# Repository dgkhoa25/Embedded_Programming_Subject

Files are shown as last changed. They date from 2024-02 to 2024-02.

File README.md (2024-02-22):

This project is created based on the subject named "Embedded Programming" (Lập trình nhúng).

The name of project is "Designing a remote vehicle control model via rf and bluetooth protocol".

******************************** ABSTRACT ********************************

  - Helps in basic understanding of ST microcontrollers by controlling single components such as motor control, multi-state programming, and wireless communication setup.
  - Create a general overview model so we can visualize the design for an embedded system, which is essentially just simple parts assembled to suit.
  - Give team members the opportunity to learn basic wireless protocol standards and hardware programming for the system.

******************************** VIDEO DEMO ********************************
 
Link Youtube: https://youtu.be/idwfzNZjZEc?si=ZoLyBULExPPUORM8

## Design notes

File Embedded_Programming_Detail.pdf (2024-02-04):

Báo cáo đồ án Lập trình nhúng

THIẾT KẾ MÔ HÌNH ĐIỀU KHIỂN XE TỪ XA

THÔNG QUA GIAO THỨC RF VÀ BLUETOOTH

Danh sách sinh viên thực hiện

Họ và tên: | Mã số sinh viên

▪

### 1. Giới thiệu (2đ)

### 1.1 Mục đích đề tài:

- Nhằm ôn lại kiến thức đã học trên lớp để thiết kế một mô hình xe có thể điều khiển thông qua hai giao thức là RF và Bluetooth.
- Nhằm tìm hiểu các ngoại vi thông dụng khác của vi điều khiển STM32F103C8T6 như UART, SPI, ADC…. Đồng thời, tìm hiểu thêm cách thức truyền thông không dây cơ bản cho một hệ thống nhúng.
- Nhằm thực hiện mô hình hóa ý tưởng điều khiển xe ô tô thông qua các giao thức chuẩn cơ bản. Cũng như sau này, là nền tảng để bắt đầu trong lĩnh vực Automotive.

1.2 Ý nghĩa đề tài:

- Giúp cho việc hiểu cơ bản về vi điều khiển của hãng ST bằng cách điều khiển các thành phần đơn như điều khiển động cơ, lập trình nhiều trạng thái, thiết lập truyền thông không giây.
- Tạo mô hình khái quát chung để chúng ta có thể hình dung về việc thiết kế cho một hệ thống nhúng, bản chất chỉ là những phần đơn giản lắp ghép lại sao cho phù hợp.
- Giúp các thành viên trong nhóm có cơ hội tìm hiểu các chuẩn giao thức không dây cơ bản và lập trình phần cứng cho hệ thống.

### 2. Cơ sở lý thuyết (2đ) 2.1 Hệ thống xung clock của vi điều khiển

- Cách cấu hình xung Clock trên STMCubeMX.
- Cách chia tần số xung Clock khi cấu hình xuất xung PWM (tần số được sử dụng trong đề tài là 1 kHz).
- Cách thức hoạt động của ngắt System timer 24 bit đếm xuống.

### 2.2 Hệ thống ngoại vi của vi điều khiển

- Cách cấu hình Port/Pin vào ra trên STMCubeMX
- Cách thức hoạt động của các thanh ghi cấu hình GPIO như thanh ghi CRL, CRH, BSRR…
- Cách đọc các trạng thái phím nhấn cũng như mức logic ở các ngõ vào/ra sao cho phù hợp với mức logic của vi điều khiển.

### 2.3 Hệ thống truyền thông

- Hiểu cơ bản cách hoạt động của các bộ UART, SPI để cấu hình và sử dụng các hàm từ thư viện HAL

- Cách thức truyền nhận một chuỗi và xử lí chuỗi để thực hiện các công việc điều khiển.

### 2.4 Hệ thống ngoại vi Analog/Digital Convert

- Hiểu được cách hoạt động của bộ ADC và các cách đọc từng kênh.
- Thực hiện mapping giá trị vào các ngưỡng.

### 2.5 Hệ điều hành nhúng Embedded Operating System

- Hiểu cách cấu hình và chọn giá trị khoảng thời gian cho các tiến trình(TASK)

### 3. Thiết kế phần cứng (2đ) 3.1 Sơ đồ khối:

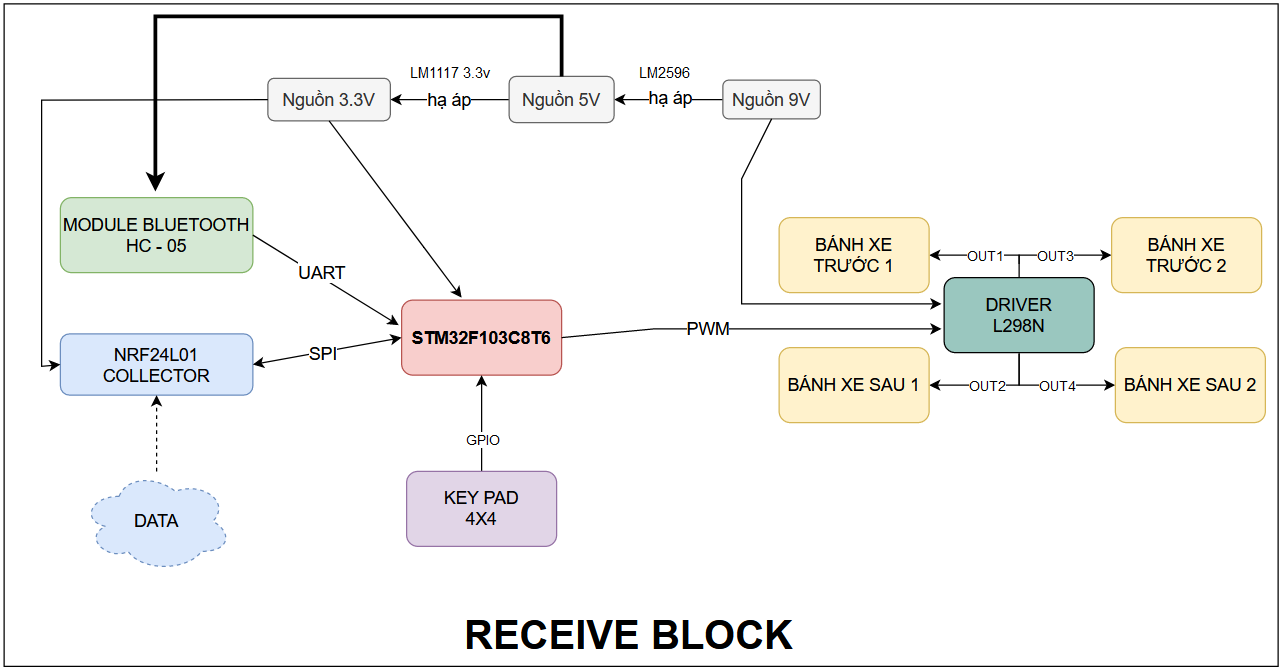
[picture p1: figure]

Hình 1: Sơ đồ khối của khối nhận sử dụng STM32F103C8T6

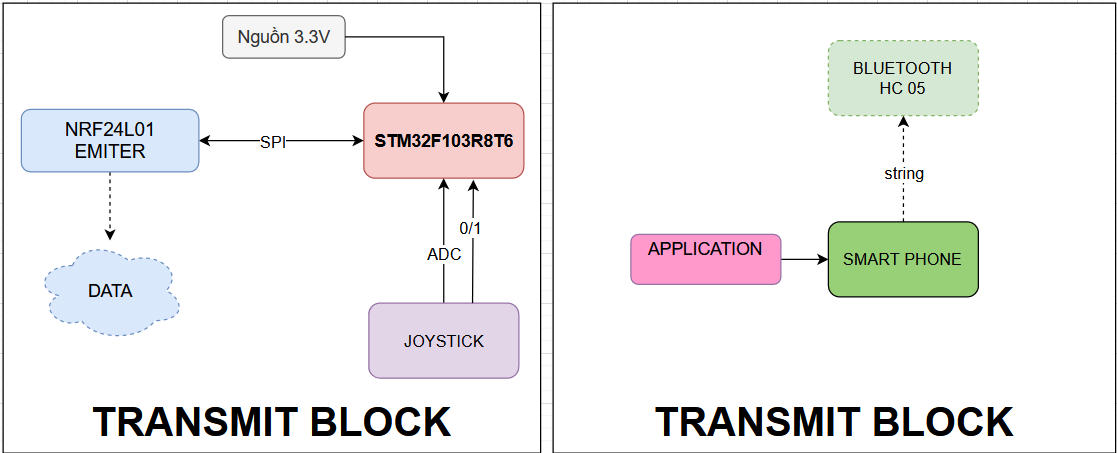
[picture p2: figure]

Hình 2: Sơ đồ khối của hai khối truyền dữ liệu sử dụng STM32F103R8T6 Giải thích sơ đồ khối: gồm có 2 khối chính là khối nhận và khối truyền dữ liệu
3.1.1 Khối nhận và xử lí tín hiệu:
- Khối nguồn: Sử dụng nguồn pin 9V để cấp cho 4 động cơ giảm tốc, tiếp tục hạ áp từ 9V xuống 5V để cấp cho module Bluetooth HC 05, tiếp tục thực hiện hạ áp từ 5V xuống 3.3V đê cấp cho vi điều khiển STM32F103C8T6 và module NRF24L01.
- Khối Vi điều khiển STM32F103C8T6: Vi điều khiển thực hiện nhận tín hiệu không dây và xử lí các tiến trình như kiểm tra KEYPAD, phân tích chuỗi kí tự, định thời chương trình, băm xung PWM…
- Khối Blutooth HC05: nhận chuỗi tín hiệu từ ứng dụng điều khiển trên điện thoại và thực hiện gửi vào vi điều khiển thông qua giao thức UART.
- Khối NRF24L01: nhận tín hiệu từ khối truyền và thực hiện gửi chuỗi kí tự thông qua giao thức SPI.
- Khối Driver L298N: nhận tín hiệu xung PWM từ vi điều khiển để cho ra dải điện áp khác nhau làm thay đổi tốc độ động cơ.
3.1.2 Khối truyền tín hiệu:
- Khối nguồn: nguồn cấp 3.3V lấy từ USB mạch nạp ST-Link V2.
- Khối vi điều khiển STM32F103R8T6: Vi điều khiển thực hiện gửi chuỗi kí tự điều hướng dựa vào tiến trình xử lí Joystick. Joystick sẽ được đọc tín hiệu vào MCU thông qua kênh ADC 12 bit và một nút nhấn tích hợp sẵn trên Joystick để thực hiện chuyển đổi qua lại giữa 2 sóng Blutooth và RF.
- Khối Smartphone: được cài sẵn ứng dụng Bluetooth RC Controller. Khi kết nối với thành công với điện thoại sẽ bấm các nút điều hướng trên giao diện để gửi chuỗi kí tự xuống HC 05.

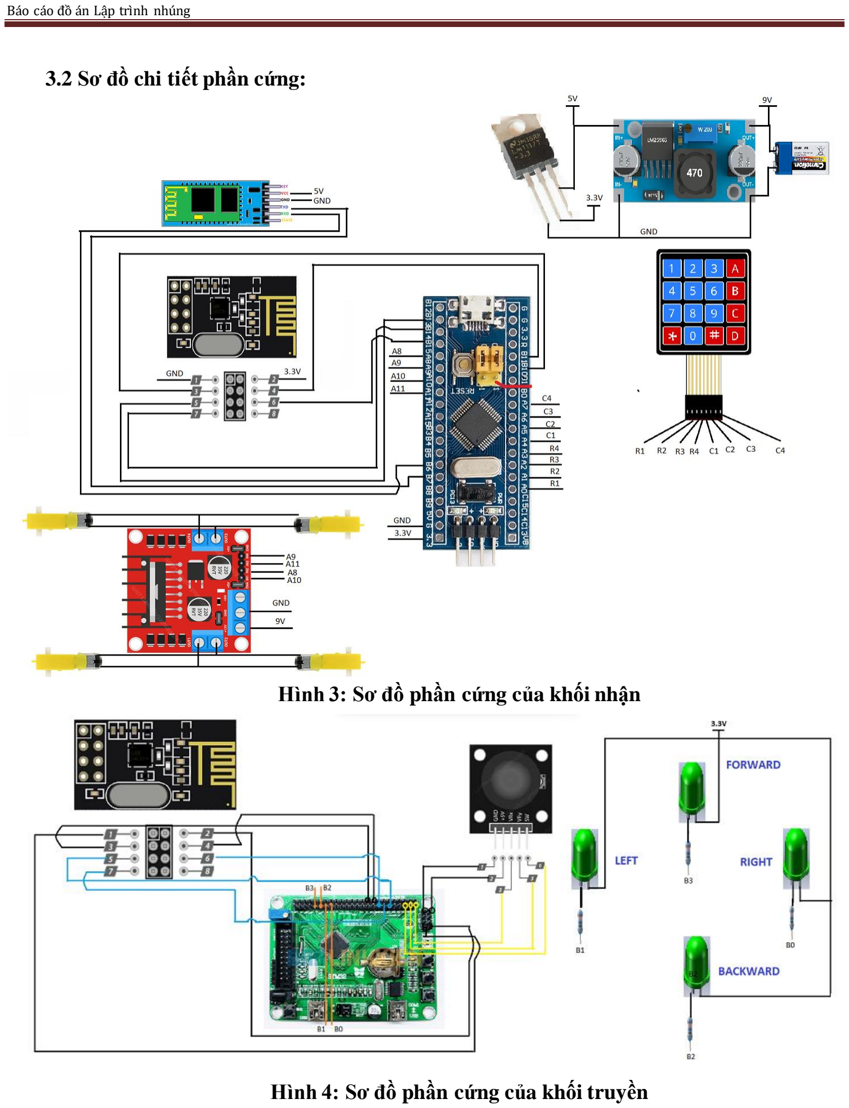
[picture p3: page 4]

### 3.2 Sơ đồ chi tiết phần cứng:

Hình 3: Sơ đồ phần cứng của khối nhận

Hình 4: Sơ đồ phần cứng của khối truyền

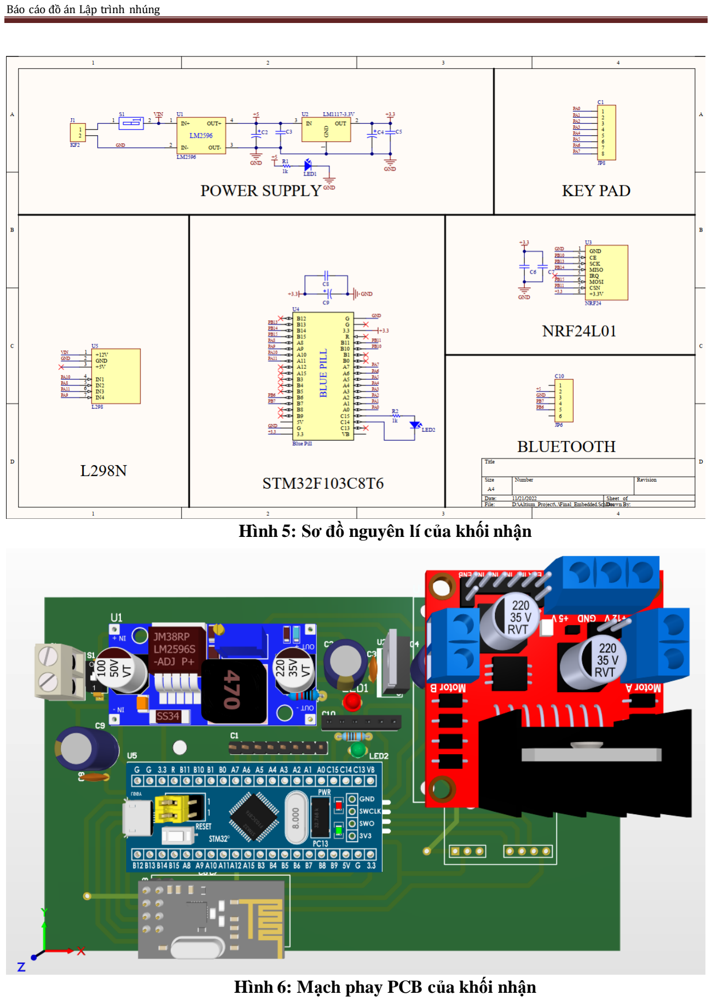
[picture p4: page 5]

Hình 5: Sơ đồ nguyên lí của khối nhận

Hình 6: Mạch phay PCB của khối nhận

Giải thích sơ đồ nguyên lí:
- Khối nguồn cấp vào: sử dụng 2 pin Li-on 4.2V cấp nguồn cho driver L298. Qua mạch hạ áp LM2596 còn 5V để cấp cho Bluetooth HC 05. Tiếp tục hạ áp qua LM1117-3.3V để cấp cho vi điều khiển và NRF24L01.
- Khối vi điều khiển STM32F103C8T6:
+ Các chân A0 – A3(Output), A4 - A7(Input) dùng cho chức năng quét KEYPAD 4x4 + Các chân A8 nối với IN2, A9 nối với IN4, A10 nối với IN1, A11 nối với IN3 trên driver L298.
+ Chân A7 nối với Rx, chân A6 nối với Tx của moudule Bluetooth HC 05.
+ Chân B10 nối với chân CE, B11 nối với chân CSN, B13 nối với chân SCK, B14 nối với chân MISO, chân B15 nối với chân MOSI của module NRF24L01.
+ Chân C14 và C15 mắc nối tiếp với 1 LED và 1 điện trở để tạo tín hiệu khi cần.

### 4. Thiết kế phần mềm (2đ) 4.1 Lưu đồ chương trình trạm thu – Receive Blcok:

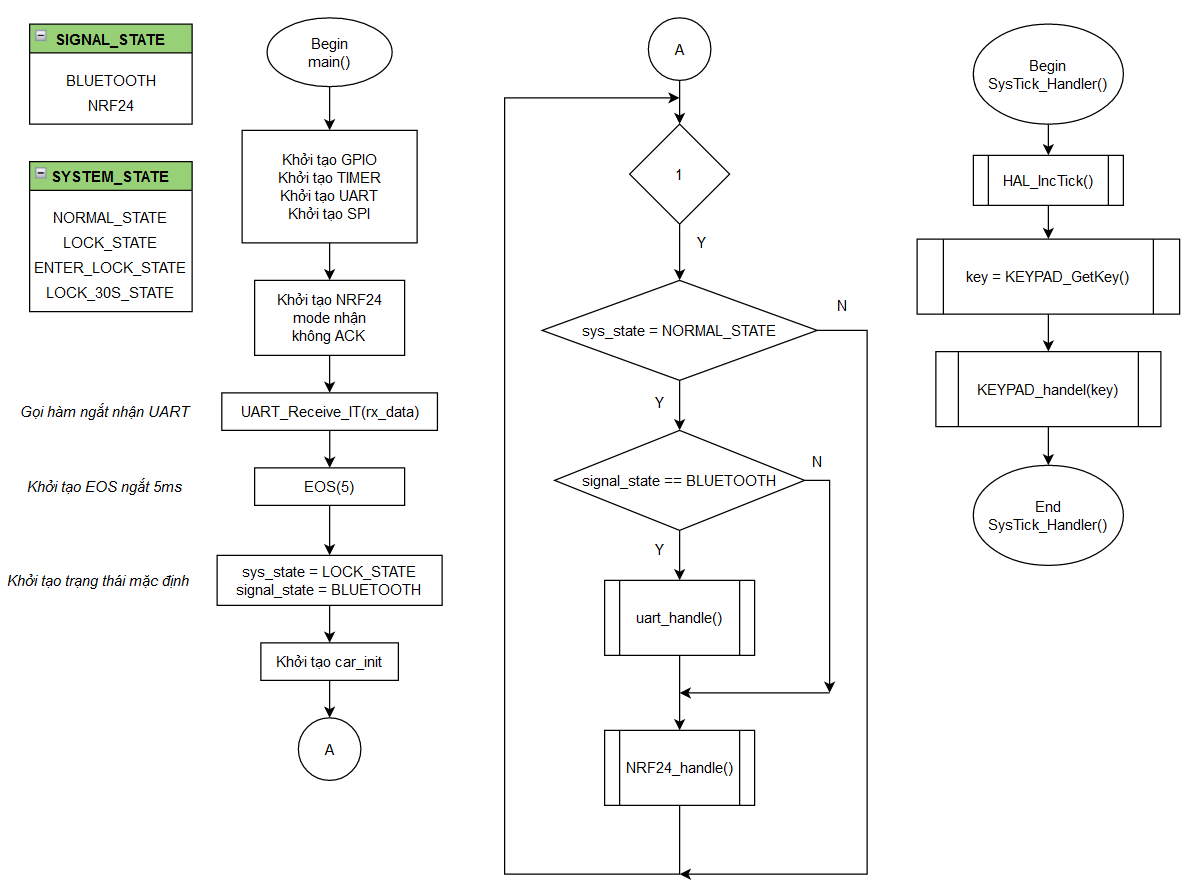
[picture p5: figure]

Hình 7: Lưu đồ chương trình chính trong file main.c (1) Giải thích: Hệ thống sẽ chờ được mở khóa(NORMAL_STATE) để tiếp nhận các tín hiệu điều khiển. Ngoài ra hệ thống còn khởi tạo hệ điều hành nhúng EOS với chu kỳ ngắt 5ms để thực hiện quét KEYPAD và các hàm thực thi KEYPAD.
Mặc định hệ thống sẽ được điều khiển thông qua tín hiệu Bluetooth. Nếu nút nhấn trên Transmit Block được nhấn thì sẽ chuyển sang điều khiển tín hiệu NRF24 và ngược lại.

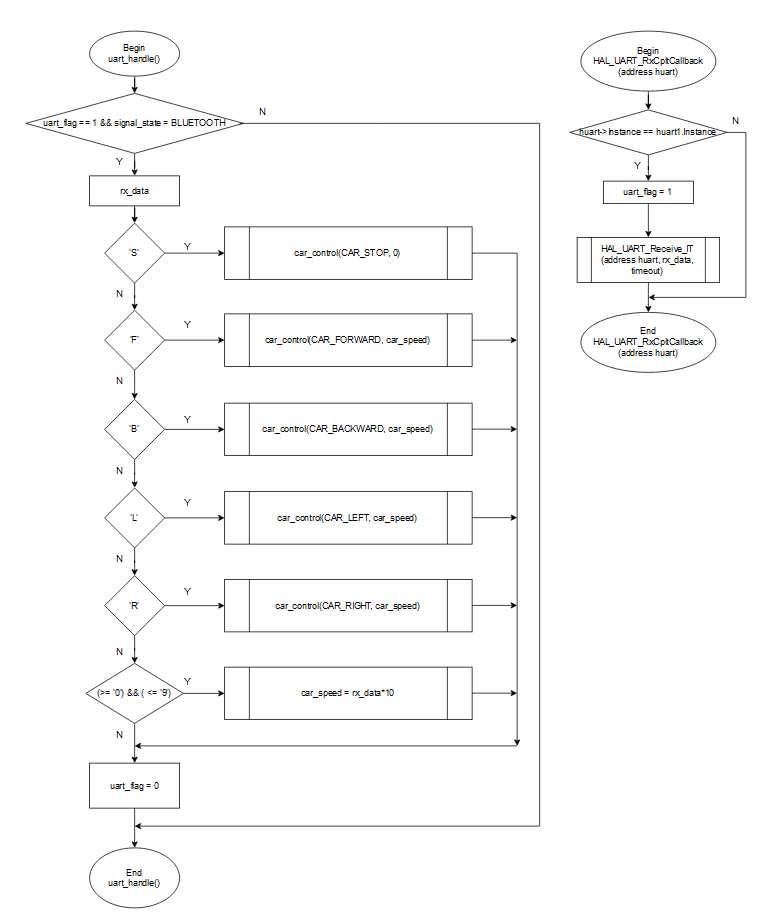
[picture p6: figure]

Hình 8: Lưu đồ chương trình con trong file main.c (2) Giải thích: Chương trình này sẽ kiểm tra biến cờ(uart_flag) nhận dữ liệu và có đang ở trong trạng thái tín hiệu điều khiển bằng Bluetooth không. Nếu cả 2 đúng thì thực hiện giải mã dữ liệu từ UART gửi đến. Hình bên trái là hàm ngắt nhận UART khi có kí tự gửi đến sẽ xảy ra ngắt, gán vào biến rx_data và đặt cờ uart_flag = 1.

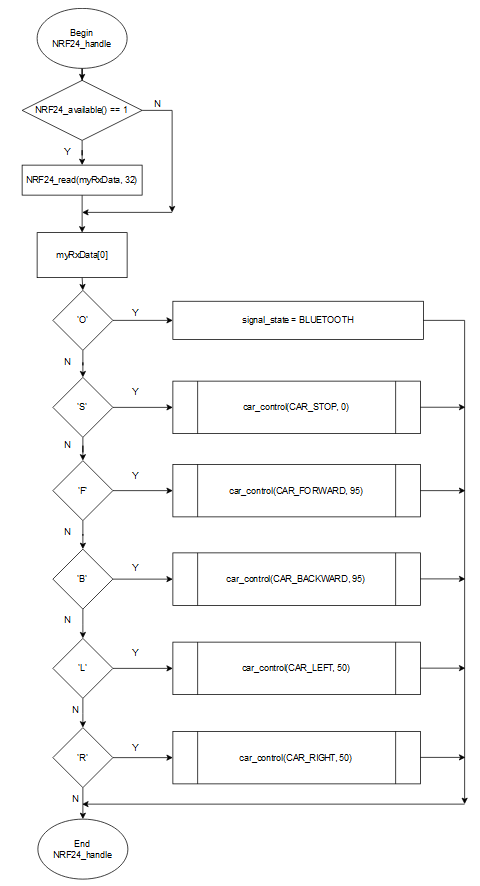
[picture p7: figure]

Hình 9: Lưu đồ chương trình con trong file main.c (3) Giải thích: Chương trình này sẽ lắng nghe có tín hiệu NRF24 gửi đến hay không (hàm NRF24_available()), nếu có tín hiệu thì sẽ thực hiện giải mã kí tự đã nhận để điều khiển xe. Do khối Transmit Block đã cấu hình gửi 1 kí tự nên chỉ cần sử dụng dữ liệu mảng đầu tiên để thực hiện điều khiển. Kí tự ‘O’ để hệ thống bật chế độ điều khiển Bluetooth.

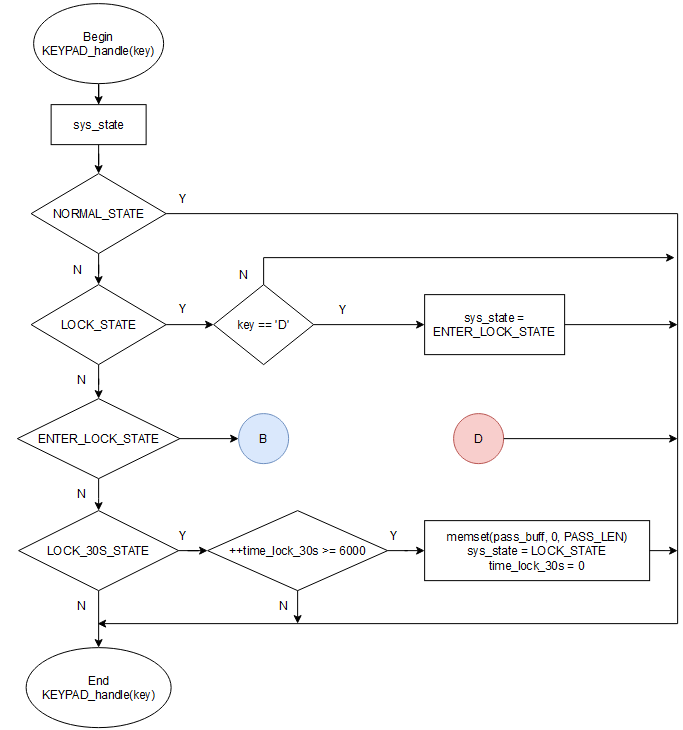
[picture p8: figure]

Hình 10: Lưu đồ chương trình con trong file main.c (4) Giải thích: Chương trình này dùng để nhập mật khẩu khởi động xe. Với mật khẩu được định nghĩa sẵn là “12345678”. Khi nhấn phím D thì sẽ vào trạng thái cho phép nhập mật khẩu. Khi đã vào trạng thái ENTER_LOCK_STATE sẽ thực hiện các công việc được trình bày riêng ở phần tiếp theo. Nếu mật khẩu đúng thì sẽ mở khóa xe(NORMAL_STATE), nếu sai thì xe sẽ bị khóa 30 giây. Khi 30 giây kết thúc quay lại trạng thái LOCK_STATE, đồng thời thực hiện reset giá trị các phần tử trong mảng bằng hàm memset để chờ nhập mật khẩu mới.

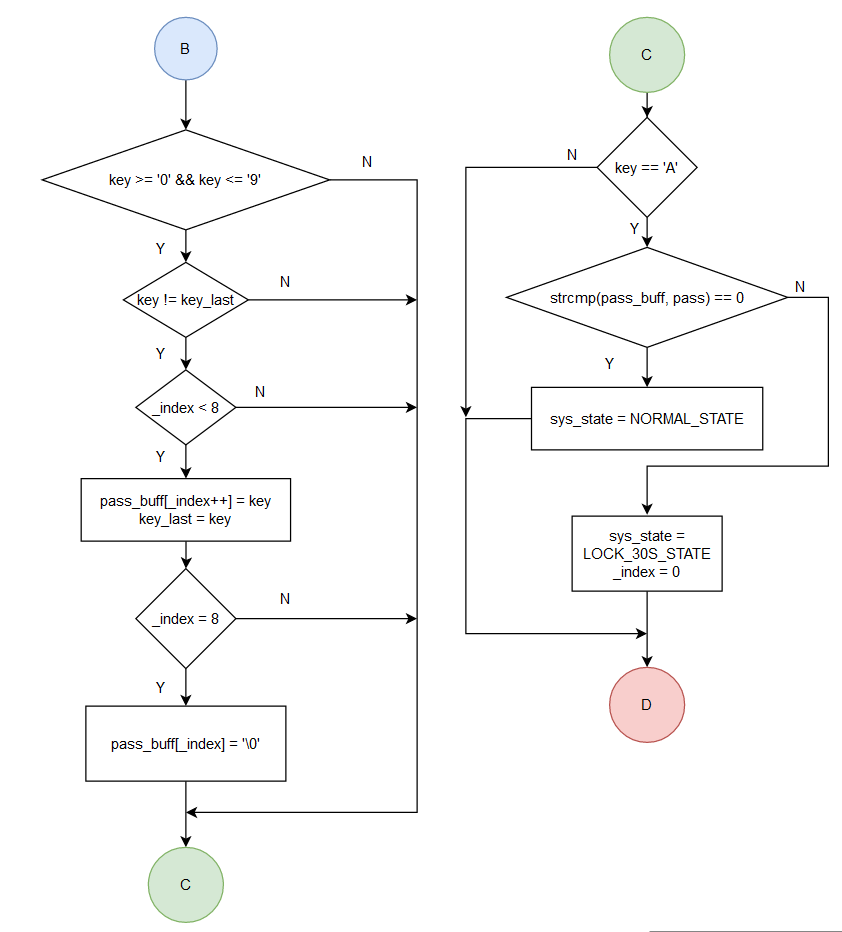
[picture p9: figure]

Hình 11: Lưu đồ giải thuật chương trình con trong file main.c (5) Giải thích: Chương trình này thực hiện đọc giá trị biến key để tiến hành đẩy kí tự vào một mảng đệm (hay mật khẩu của người dùng nhập) gồm 8 phần tử và thêm một phần tử thứ 9 là ‘\0’ để tạo thành một chuỗi. Sau đó nhấn phím A để kiểm tra và sử dụng hàm strcmp trong thư viện string.h để so sánh. Nếu mật khẩu định nghĩa sẵn và mật khẩu đã nhập đúng thì thực hiện mở khóa(NORMAL_STATE), nếu sai thì chuyển sang trạng thái LOCK_30S_STATE.

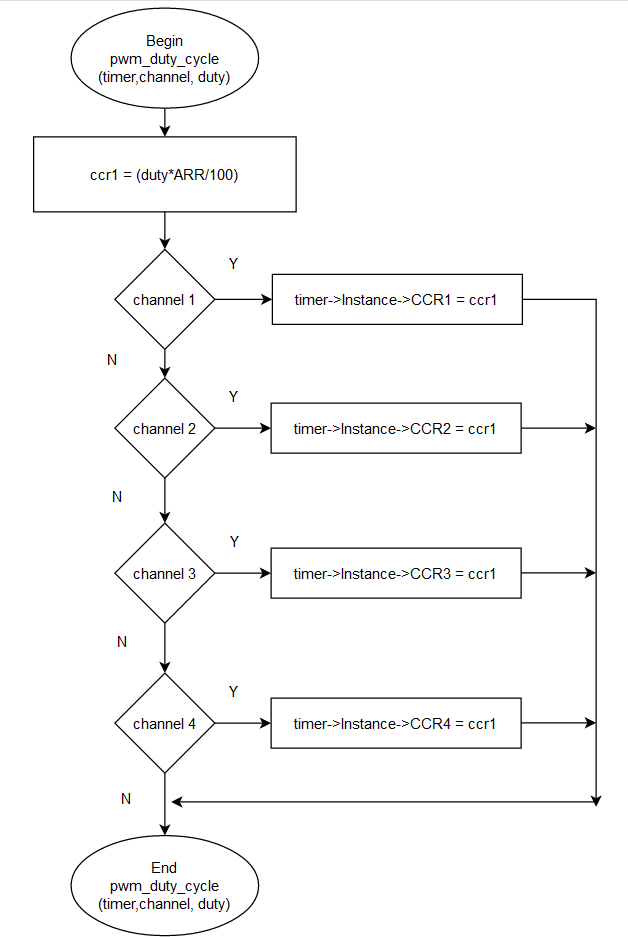
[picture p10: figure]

Hình 12: Lưu đồ giải thuật chương trình con trong file pwm.c Giải thích: Chương trình con này sẽ thực hiện, đọc vào giá trị duty từ 0 đến 100 để đặt giá trị thanh ghi CCR1 (kênh 1). Mục đích là để gán các số từ 0 đến 100 ứng với từ 0 đến 999 (PWM tần số 1 kHz) cho thanh ghi CCR1 để làm thay đổi độ rộng xung.

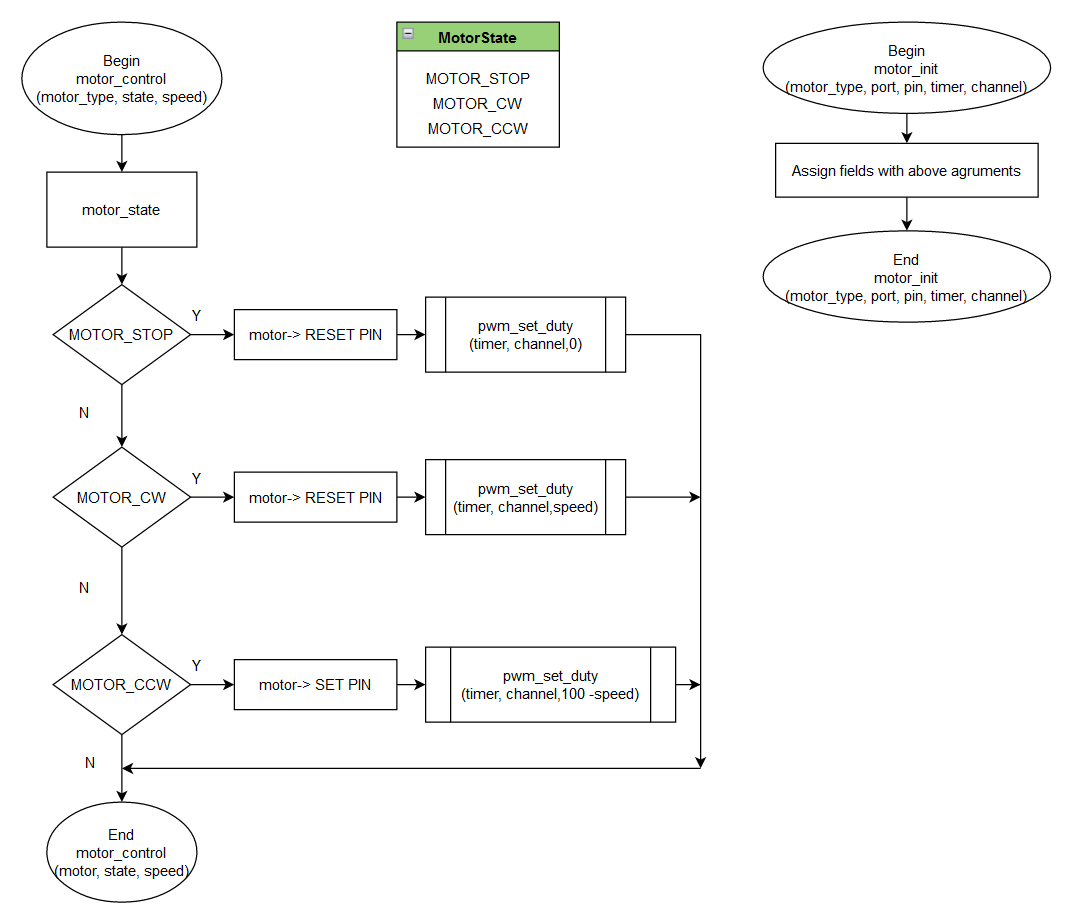
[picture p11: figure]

Hình 13: Lưu đồ giải thuật chương trình con trong file Motor.c Giải thích: Chương trình con này kiểm tra trạng thái được truyền vào để thực hiện điều khiển động cơ quay theo chiều ở trạng thái đó. Có 3 trạng thái cho một Motor là STOP(Dừng), CW(quay theo chiều kim đồng hồ) và CCW(quay theo ngược chiều kim đồng hồ). Ngoài ra chương trình còn được truyền vào biến tốc độ speed để điều chỉnh tốc độ theo mong muốn. Giải thích thêm với module L298 ta cần 2 chân(IN1 và IN2) để thực hiện đảo chiều quay và điều chỉnh tốc độ cho 1 motor ở ngõ ra OUT1 và OUT2.Do đó cần một chân xuất tín hiệu Output và một chân xuất xung PWM từ vi điều khiển STM32F103C8T6. Tương tự cho với IN3 và IN4.

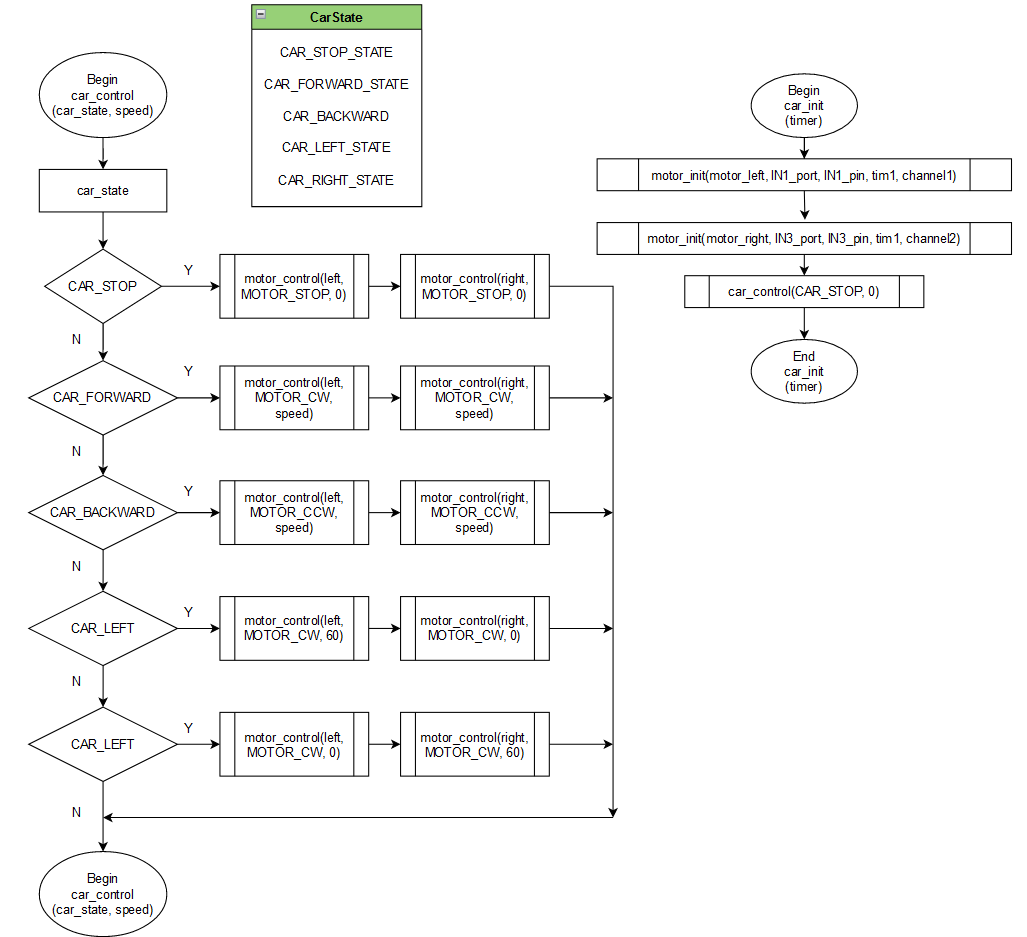
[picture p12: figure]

Hình 14: Lưu đồ giải thuật chương trình con trong file car.c Giải thích: Chương trình con này kiểm tra trạng thái được truyền vào để điều khiển hướng xe. Với một xe có 5 trạng thái được định nghĩa như sau: STOP(Dừng), FORWARD(chạy tới), BACKWARD(chạy lùi), LEFT(rẽ trái), RIGHT(rẽ phải). Ứng với mỗi trạng thái sẽ gọi hàm điều khiển motor. Với 2 đối tượng motor left và motor right ta sẽ điều hướng được xe theo tín hiệu điều khiển. Bên cạnh đó trước khi điều hướng xe, ta phải khởi tạo trạng thái ban đầu cho xe(hàm car_init) ở trạng thái mặc định là STOP.

### 4.2 Các đoạn mã lệnh chính trạm thu – Receive Block:

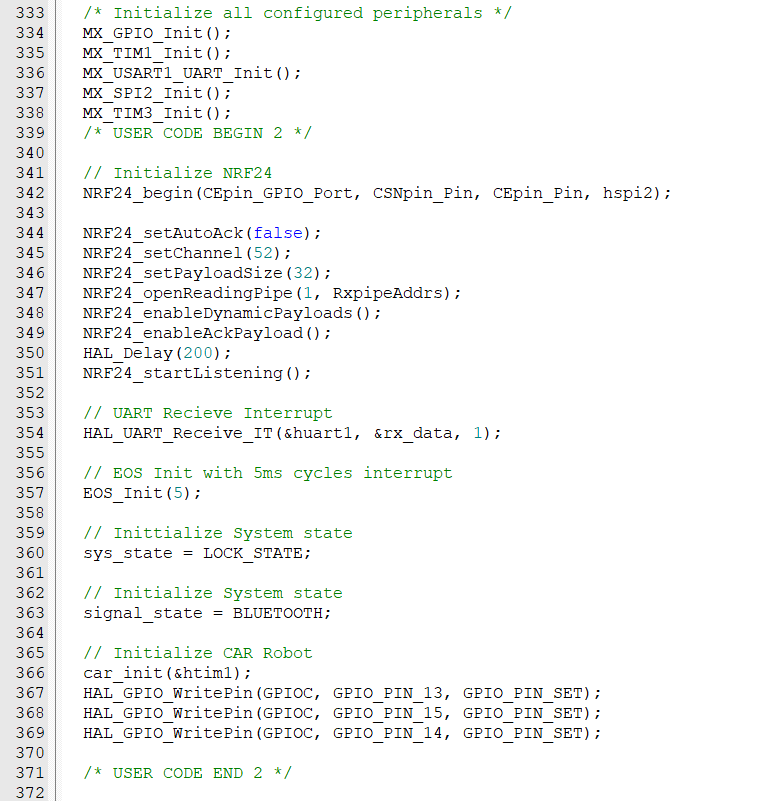
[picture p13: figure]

Hình 15: Đoạn mã lệnh khởi tạo trạng thái mặc định Giải thích:
+ Khởi tạo NRF24L01: hàm begin sẽ thực hiện khởi tạo các port và pin cho module NRF24 bao gồm 5 chân: CE, CSN, SCK, MISO, MOSI. Hàm bật acknowldge từ slave gửi về master(trong đồ án không bật – false). Hàm đặt kênh tần số cho NRF24 là 52. Hàm đặt kích thước payload (dữ liệu được chứa để truyền/nhận) là 32 byte. Hàm mở cổng nhận. Hàm bật payload động khi cần sử dụng đến và hàm bật Ackpayload. Cuối cùng là hàm bật chức năng lắng nghe(chờ dữ liệu gửi đến).
+ Khởi tạo EOS với chu kỳ ngắt 5ms và khởi tạo các trạng thái mặc định.

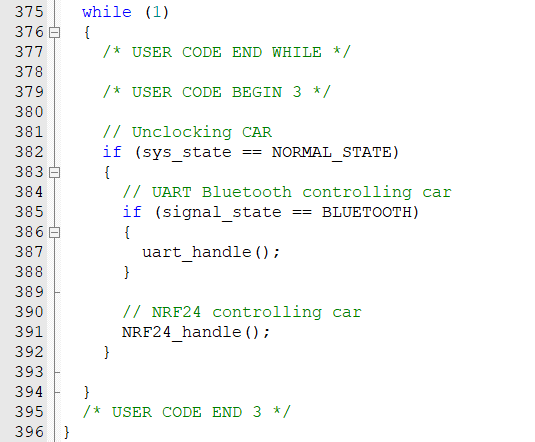
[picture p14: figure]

Hình 16: Đoạn mã lệnh chương trình trong vòng lặp vô hạn while(1)
Giải thích: Trong vòng lặp vô hạn, ta liên tục thực hiện quét trạng thái của hệ thống và trạng thái của tín hiệu. Mặc định là điều khiển bằng Bluetooth nếu có tín hiệu từ khối truyền thì sẽ chuyển sang tín hiệu NRF24.

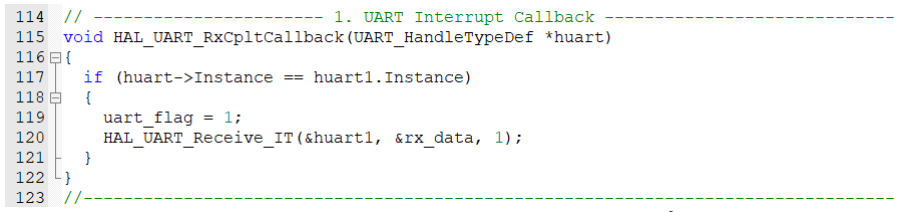
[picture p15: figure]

Hình 17: Đoạn mã lệnh trong hàm xử lí ngắt UART Giải thích: Hàm này sẽ thực thi khi có một kí tự được gửi đến thông qua Bluetooth -> UART -> vi điều khiển. Biến cờ flag đặt lên 1 để báo hiệu có 1 kí tự được gửi đến cho hàm uart_handle biết thực hiện các chức năng khác.

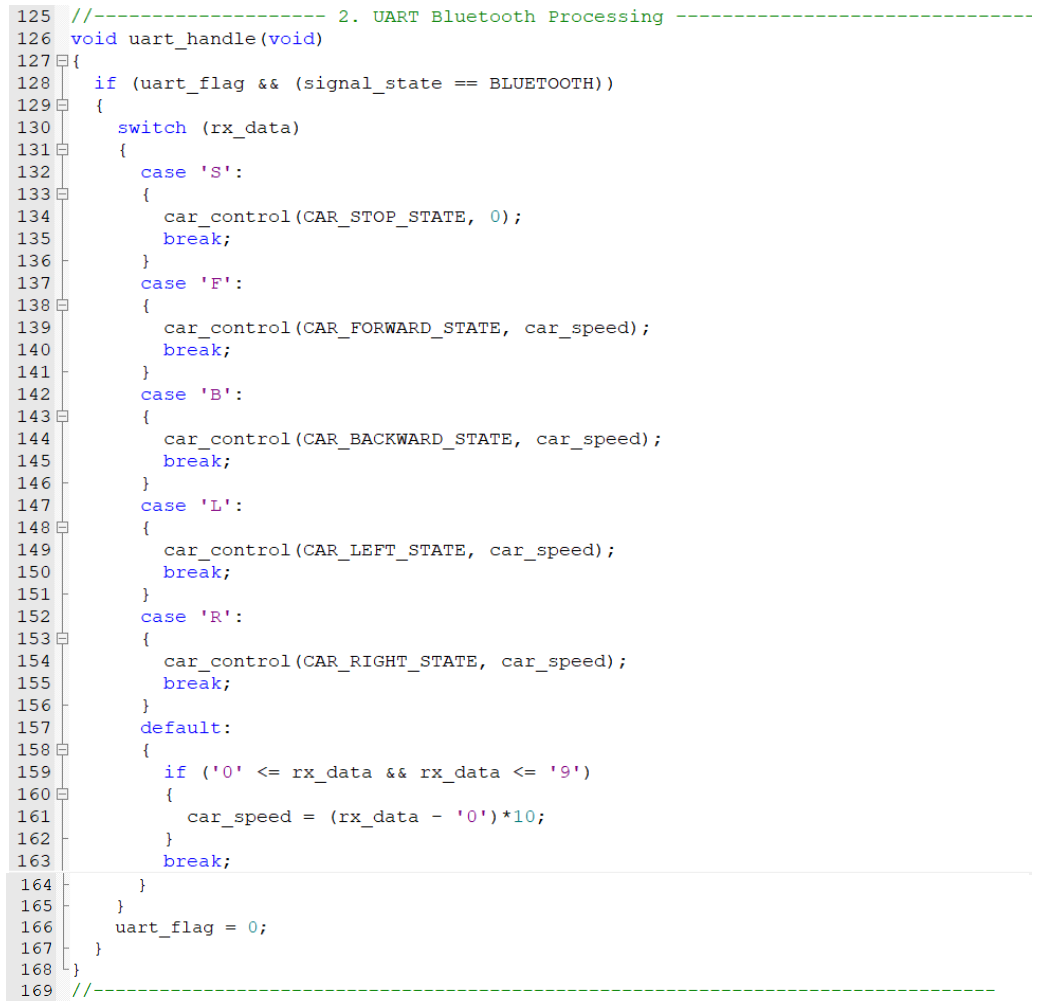
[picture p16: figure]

Hình 18: Đoạn mã lệnh hàm xử lý UART Giải thích: Hàm này thực hiện điều khiển xe thông qua Bluetooth. Với các chức năng điều khiển hướng xe và tăng giảm tốc độ.

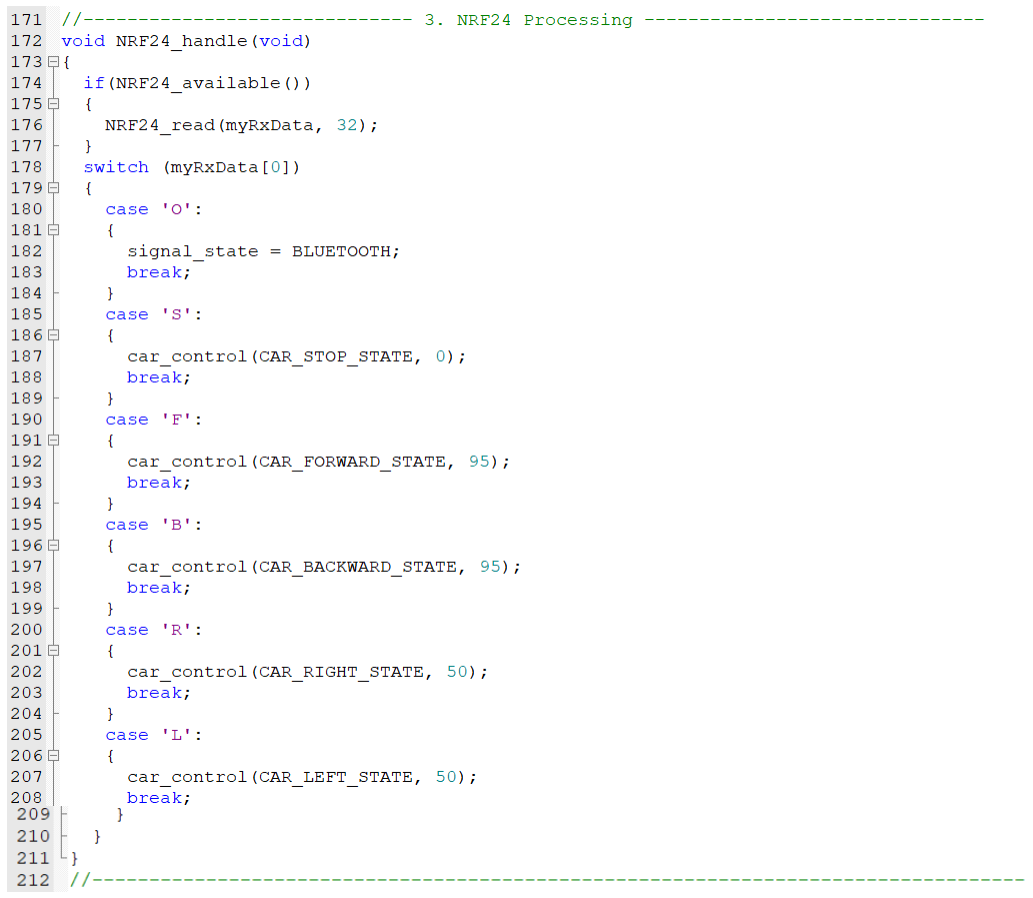
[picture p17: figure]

Hình 19: Đoạn mã lệnh hàm xử lí NRF24 Giải thích: đoạn mã lệnh này dùng để điều hướng xe theo tín hiệu NRF24. Với tốc độ được đặt sẵn trong suốt quá trình chạy không thể thay đổi.

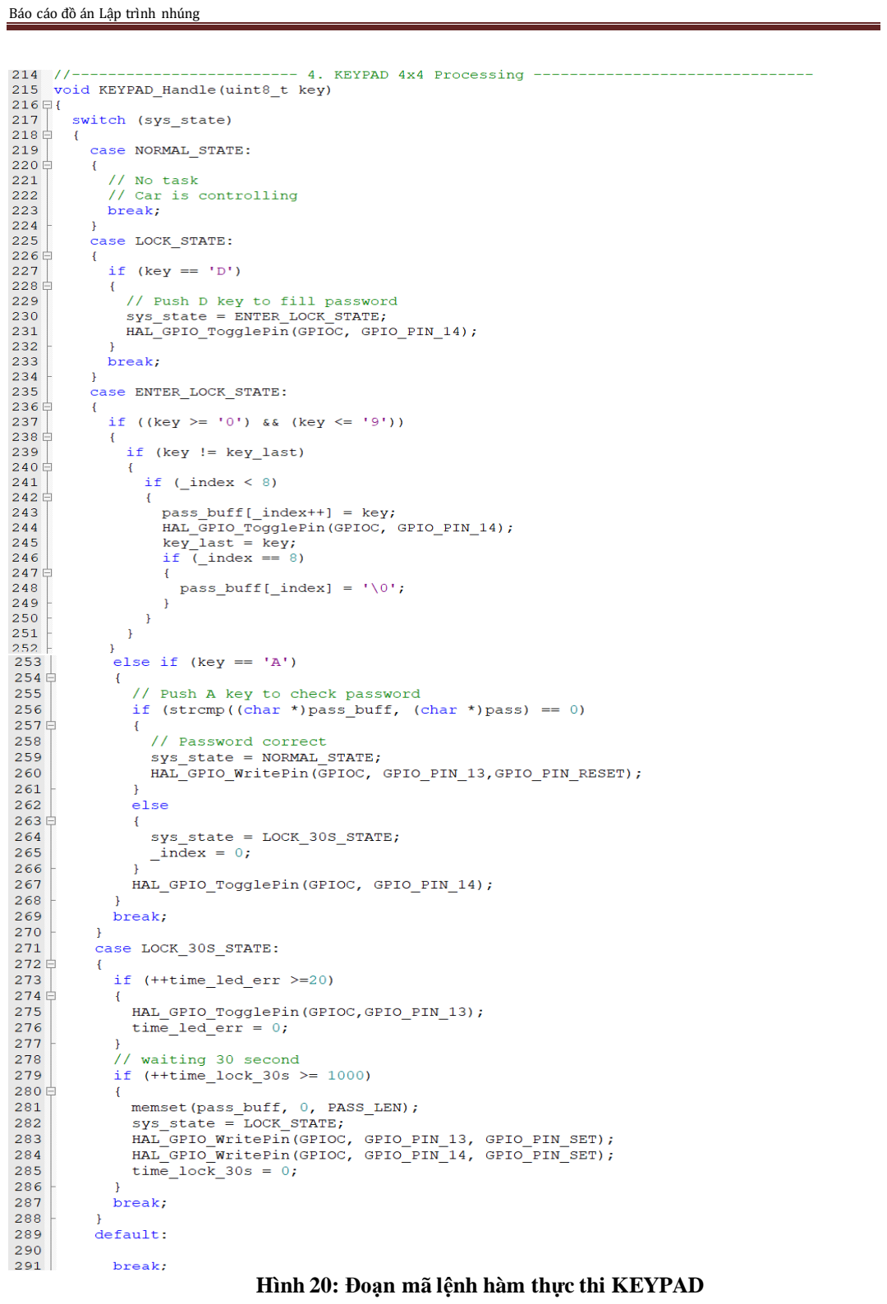
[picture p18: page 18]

Hình 20: Đoạn mã lệnh hàm thực thi KEYPAD

Giải thích: hàm này thực hiện đọc giá trị biến key truyền vào và xử lí nhập vào mảng đệm để kiểm tra mật khẩu có đúng hay không. Ngoài ra còn có thêm một số hiệu ứng LED báo
hiệu | trên | mạch | của | xe | thông | qua | các | hàm | HAL_GPIO_Writepin | và
HAL_GPIO_Togglepin.

Hình 21: Đoạn mã lệnh hàm ngắt SysTick do EOS gọi đến Giải thích: khi SysTick timer đếm được 5ms sẽ gọi hàm ngắt này 1 lần và thực hiện quét KEYPAD và thực thi các hàm KEYPAD.

### 4.3 Lưu đồ giải thuật trạm phát – Transmit Block:

Hình 22: Lưu đồ giải thuật chương trình chính trong file main.c Giải thích: Hệ thống sẽ quét qua các trạng thái để thực hiện truyền kí tự qua trạm nhận Receive Block. Nếu vào trạng thái OTHER, trạm truyền sẽ truyền kí tự ‘O’ tức cho phép điều khiển xe bằng Bluetooth. Nếu vào trạng thái JOYSTICK thì sẽ truyền các kí tự chuyển hướng S, R, L, F, B thông qua NRF24 đến trạm nhận Receive Block.
Đồng thời, quét qua hàm đọc nút nhấn để lấy sự kiện cho hàm btn_pressing_callback xử lí chuyển đổi qua lại giữa điều khiển bằng Bluetooth và NRF24.

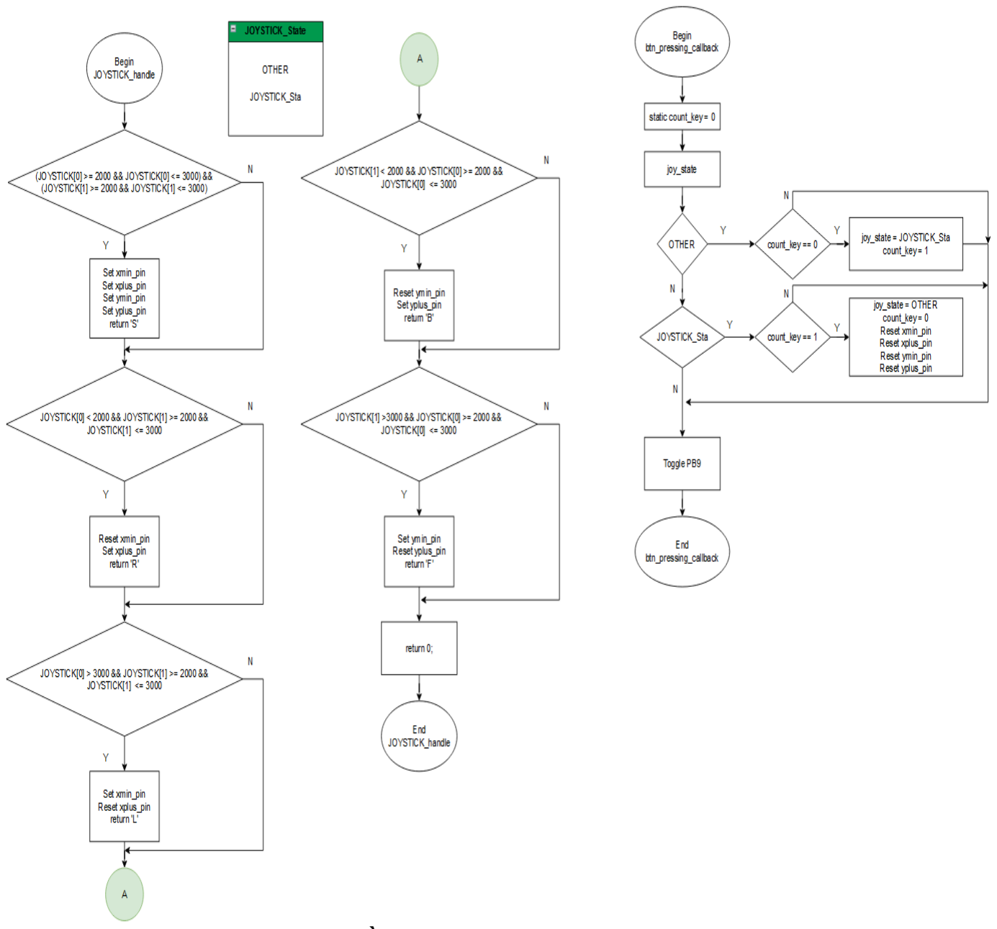
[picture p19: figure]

Hình 23: Lưu đồ giải thuật chương trình con trong file main.c Giải thích: Chương trình con này thực hiện so sánh các giá trị do bộ ADC đọc được ở cột x và y từ Joystick để bật/tắt các LED hiển thị hướng đi tương ứng và trả về kí tự để sử dụng truyền đi cho trạm nhận. Hình bên trái, nhận nút nhấn và chuyển đổi qua lai giữa 2 trạng thái OTHER(tương ứng Bluetooth) và JOYSTICK_Sta(tương ứng NRF24).

### 4.4 Các đoạn mã lệnh chính trạm truyền – Transmit Block:

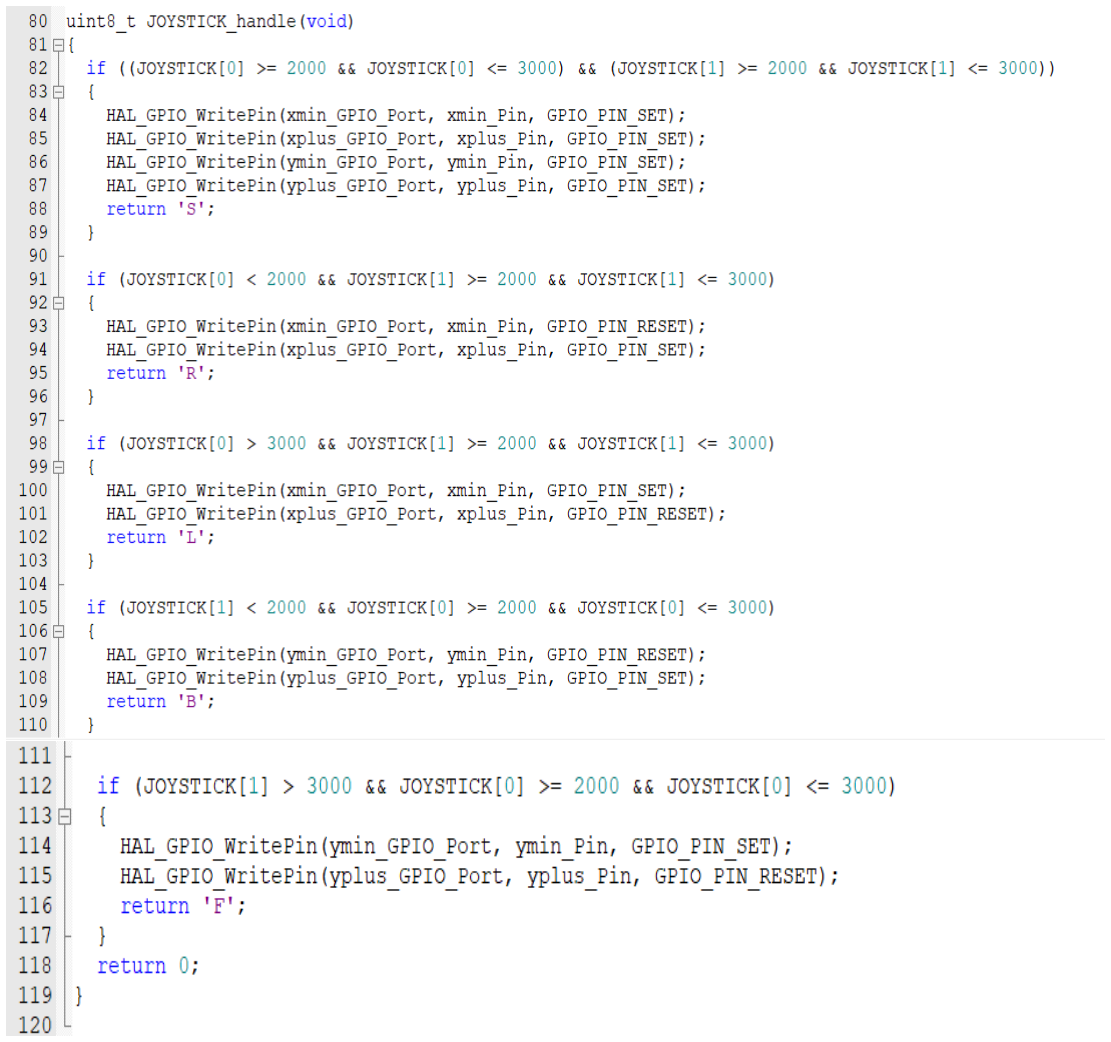
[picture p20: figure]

Hình 24: Đoạn mã lệnh hàm JOYSTICK_handle Giải thích: Giá trị ADC được lưu trong 2 phần tử của mảng. Sau đó so sánh với các mức 2000 và 3000 vì giá trị ADC khi chưa gạt Joystick nằm khoảng từ 2300 đến 2500. Nếu giá trị ADC của trục Y lớn hơn 3000 thì sẽ gửi tín hiệu chạy thẳng ‘F’, nếu nhỏ hơn 2000 thì sẽ gửi tín hiệu chạy lùi ‘B’. Tương tự với trục X lớn hơn 3000 thì sẽ gửi tín hiệu rẽ trái ‘L’, nếu nhỏ hơn 2000 thì sẽ gửi tín hiệu rẽ phải ‘R’.

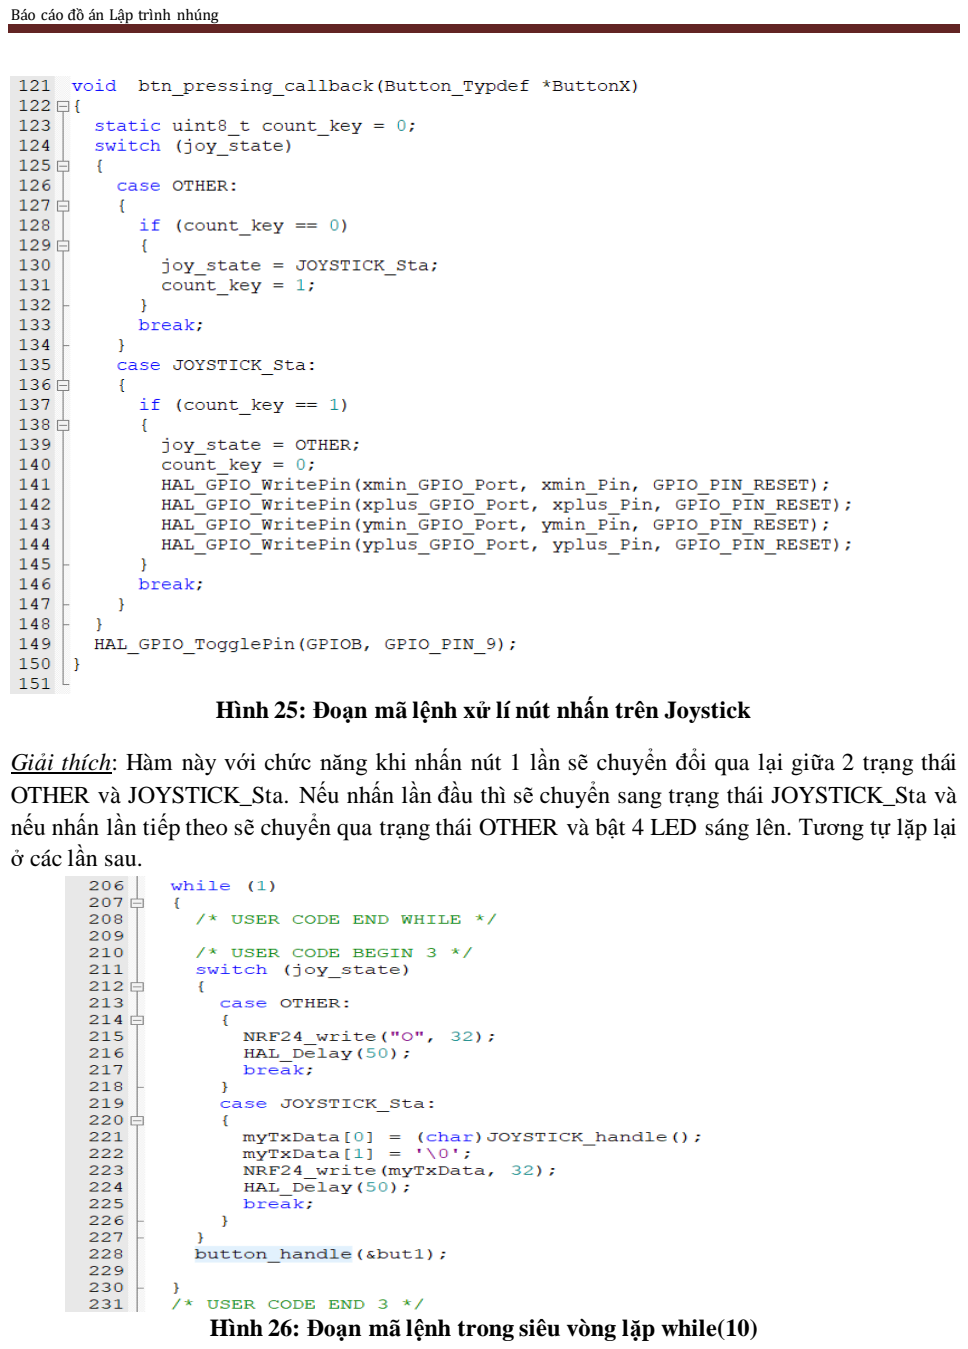
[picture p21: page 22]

Hình 25: Đoạn mã lệnh xử lí nút nhấn trên Joystick

Giải thích: Hàm này với chức năng khi nhấn nút 1 lần sẽ chuyển đổi qua lại giữa 2 trạng thái OTHER và JOYSTICK_Sta. Nếu nhấn lần đầu thì sẽ chuyển sang trạng thái JOYSTICK_Sta và nếu nhấn lần tiếp theo sẽ chuyển qua trạng thái OTHER và bật 4 LED sáng lên. Tương tự lặp lại ở các lần sau.

Hình 26: Đoạn mã lệnh trong siêu vòng lặp while(10)

Giải thích: Đoạn này sẽ thực hiện quét liên tục các trạng thái và quét phím nhấn. Nếu trạng thái là OTHER sẽ liên tục gửi kí tự ‘O’ để trạm nhận chuyển trạng thái sang Bluetooth. Nếu trạng thái là JOYSTICK sẽ thực hiện gửi các kí tự trả về từ hàm JOYSTICK_handle đến trạm nhận để điều hướng xe.

### 5. Kết quả (2đ) 5.1 Kết quả của đề tài:

- Có áp dụng lập trình nhiều trạng thái để xử lí.
- Có áp dụng hệ điều hành nhúng EOS để xử lí các tác vụ cần thiết, cũng như sử dụng quy tắc timeout (trạng thái khóa xe 30s nếu nhập mật khẩu sai).
- Về tính chuyển động của xe:
+ Chế độ Bluetooth: đáp ứng chậm hơn nhiều so với mong muốn thực tế. Thời gian trễ trong việc gửi tín hiệu rất lớn và dễ bị nhiễu.
+ Chế độ NRF24: đáp ứng nhanh và chính xác. Xe có thể di chuyển tốt trong bán kính < 15m. Hầu như không có độ trễ ở các tiến trình điều hướng xe. Độ ổn định cao hơn so với Bluetooth. Rất phù hợp cho việc thiết kế xe điều khiển cỡ nhỏ như đồ chơi trẻ em hoặc cao hơn là nghiên cứu các hệ thống cảm biến trong xe thông qua chuẩn giao tiếp này.
- Hiểu thêm về DMA cho đọc nhiều kênh ở bộ ADC và 2 giao thức truyền dữ liệu quan trọng trong đề tài là UART và SPI.

### 5.2 Khắc phục đề tài:

- Điều khiển thông qua Bluetooth: có thể module giá rẻ chưa ổn định cao. Việc xử lí tín hiệu còn thô sơ chưa qua bộ lọc nhiễu nào. Vị trí lắp đặt module trên board mạch chưa hợp lí.
Đề xuất giải pháp: có thể dùng module Bluetooth khác để thử nghiệm như các chuẩn Bluetooth Low Energy (BLE).
- Điều khiển thông qua NRF24L01: khoảng cách còn truyền còn ngắn hơn so với mong muốn là 30m.
Đề xuất giải pháp: sử dụng module có gắn thêm anten rời để tăng khuếch đại sóng RF có thể kể đến như: NRF24L01 + PA/LNA 2.4GHz Anten rời.
- Sử dụng một bộ nguồn riêng cho trạm điều khiển, không cắm mạch nạp ST Link v2.
- Thiết kế lại mạch PCB tích hợp thêm sẵn KEYPAD trên mạch, không dùng KEYPAD rời.

### 5.3 Một số hình ảnh và video demo đề tài: 5.3.1 Hình ảnh thực tế:

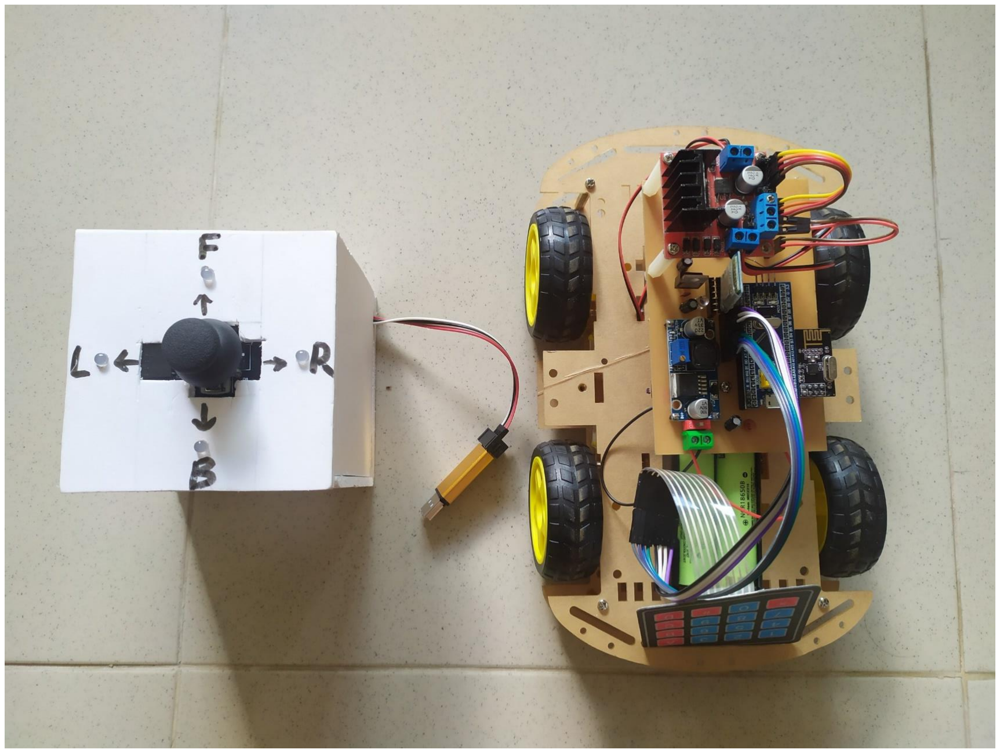
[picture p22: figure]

Hình 27. Khung xe, hệ tthống mạch điện và bộ điều khiển

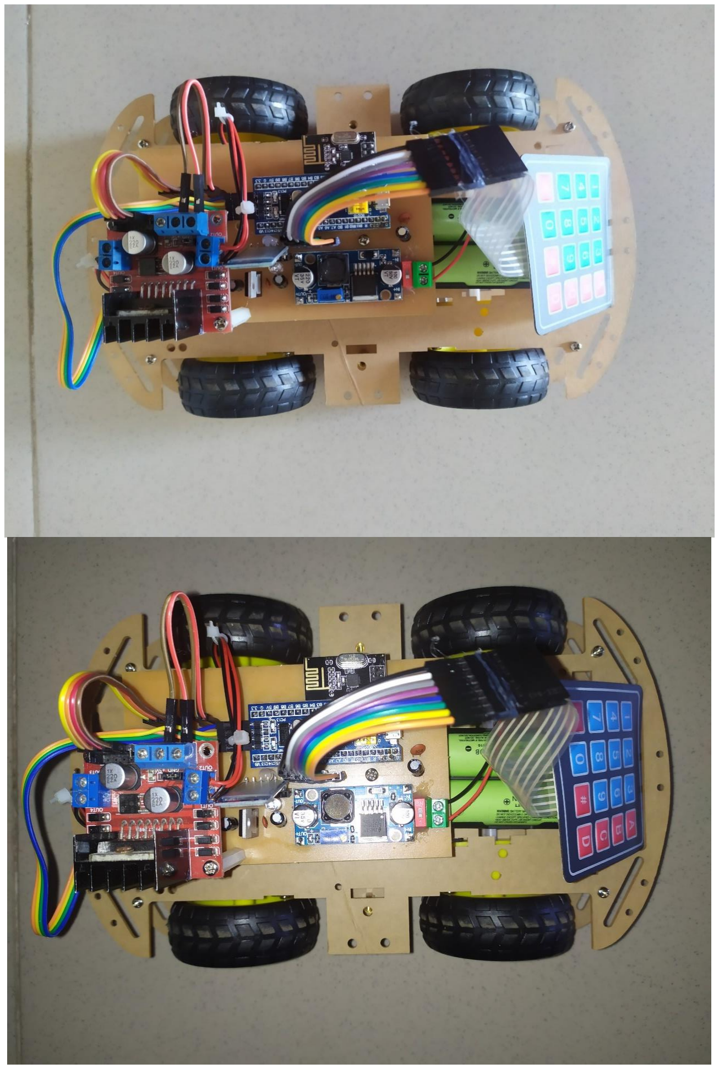
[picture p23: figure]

Hình 28. Khung xe hoàn chỉnh

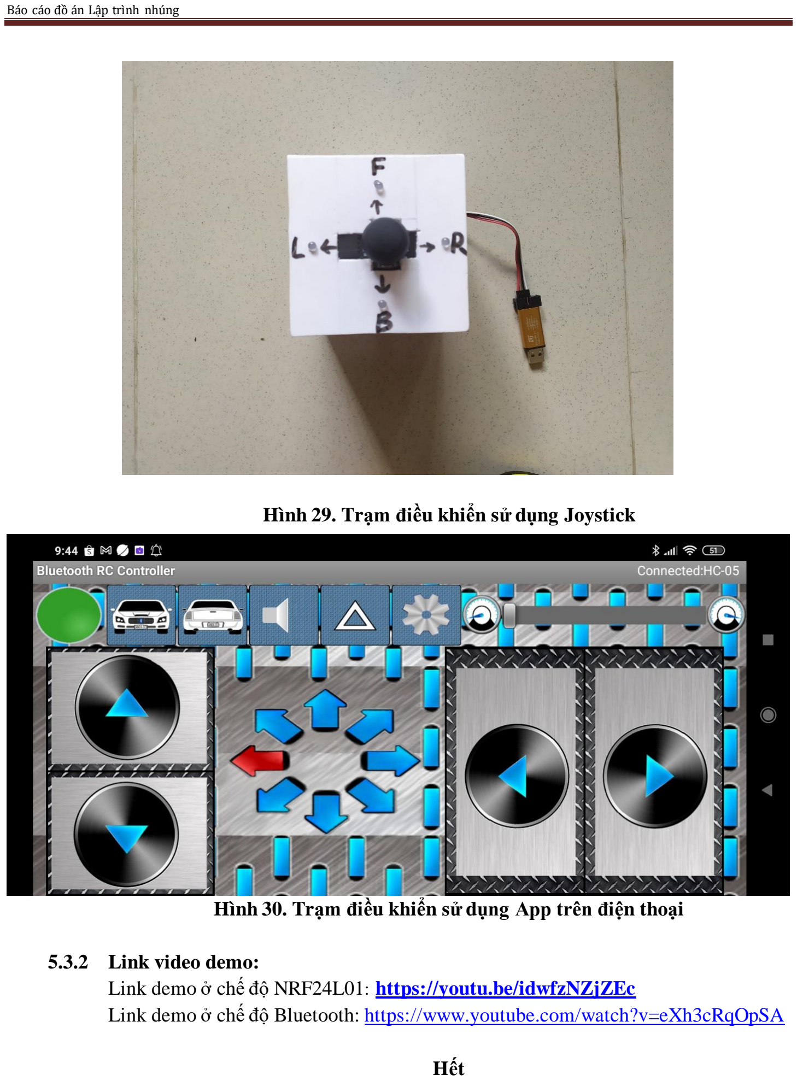
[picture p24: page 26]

Hình 29. Trạm điều khiển sử dụng Joystick

Hình 30. Trạm điều khiển sử dụng App trên điện thoại

### 5.3.2 Link video demo:

Link demo ở chế độ NRF24L01: https://youtu.be/idwfzNZjZEc
Link demo ở chế độ Bluetooth: https://www.youtube.com/watch?v=eXh3cRqOpSA

Hết

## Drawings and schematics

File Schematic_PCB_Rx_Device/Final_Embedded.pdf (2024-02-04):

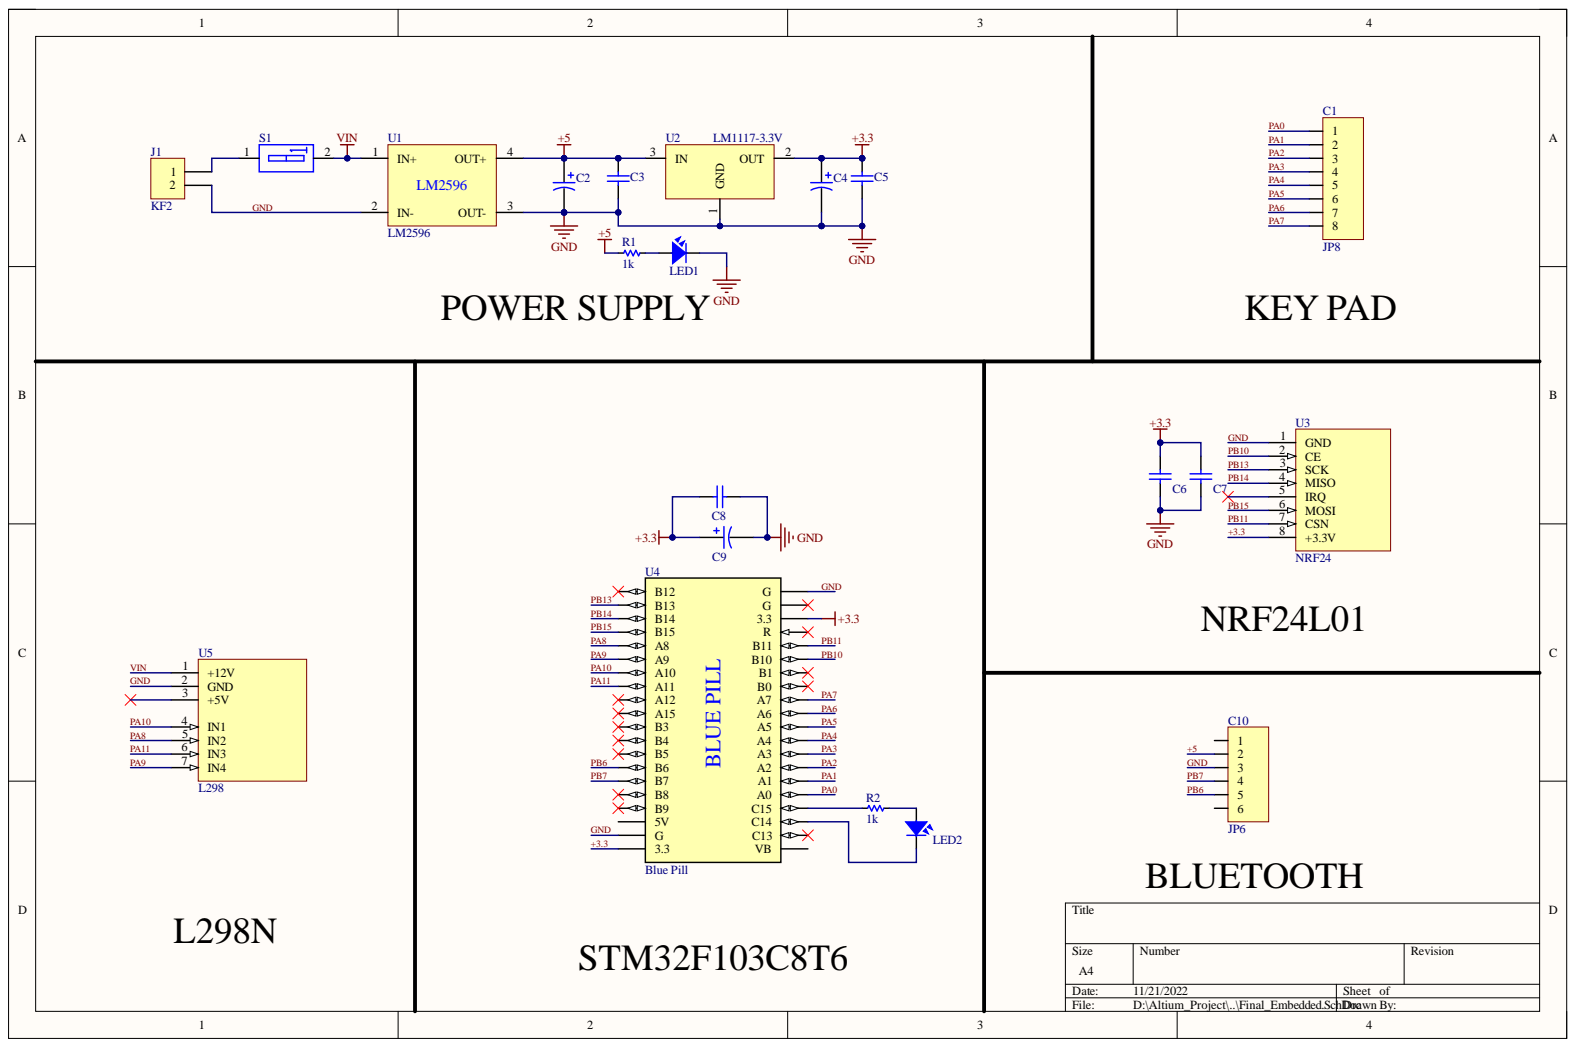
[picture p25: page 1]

Size A4 | Number | Revision

Date: 11/21/2022 | Sheet of
File: D:\Altium_Project\..\Final_Embedded.SchDDrocawn By:

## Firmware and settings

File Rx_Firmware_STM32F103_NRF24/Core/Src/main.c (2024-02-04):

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
/* Includes ------------------------------------------------------------------*/
#include "main.h"

/* USER CODE BEGIN Includes */
#include "Motor.h"
#include "Car.h"
#include "MY_NRF24.h"
#include "EOS.h"
#include "keypad.h"
#include <stdlib.h>
/* USER CODE END Includes */

/* USER CODE BEGIN PTD */

// Store the current mode of car
typedef enum
{
	BLUETOOTH = 0U,
	NRF24,
} SIGNAL_STATE;

// Store the current operation state of car
typedef enum
{
	NORMAL_STATE = 0U,	// Normal state after is unlocked
	LOCK_STATE,					// Lock state after is turned on Power
	ENTER_LOCK_STATE,		// This state is used to verify the password that input of KEYPAD
	LOCK_30S_STATE			// To car into lock state in 30 second if the password wrong
} SYSTEM_STATE;

/* USER CODE END PTD */

/* USER CODE BEGIN PD */

// The length of password
#define PASS_LEN	8

/* USER CODE END PD */

SPI_HandleTypeDef hspi2;

TIM_HandleTypeDef htim1;
TIM_HandleTypeDef htim3;

UART_HandleTypeDef huart1;

/* USER CODE BEGIN PV */

// Declare System State
static SYSTEM_STATE sys_state = LOCK_STATE;

// Declare Signal state
static SIGNAL_STATE signal_state;

// Declare UART Bluetooth variables
static uint8_t ui8_rxData;
static uint8_t ui8_uartFlag = 0;
static uint8_t ui8_carSpeed = 80;

// Declare NRF24 variables
static uint64_t ui64_rxPipeAddrs = 0x11223344AA;
static char c_myRxData[50];

// Declare KEYPAD Var
static volatile uint8_t ui8_key = 0;
static uint8_t ui8_keyLast;
static uint8_t arrui8_pass[PASS_LEN + 1] = "12345678";
static uint8_t arrui8_passBuff[PASS_LEN + 1];
static uint8_t ui8_index = 0;
static uint32_t ui32_timeLock30s = 0;
static uint32_t ui32_timeLedErr = 0;

/* USER CODE END PV */

void SystemClock_Config(void);
static void MX_GPIO_Init(void);
static void MX_TIM1_Init(void);
static void MX_USART1_UART_Init(void);
static void MX_SPI2_Init(void);
static void MX_TIM3_Init(void);
/* USER CODE BEGIN 0 */

// ----------------------- 1. UART Interrupt Callback -----------------------------
void HAL_UART_RxCpltCallback(UART_HandleTypeDef *huart)
{
	if (huart->Instance == huart1.Instance)
	{
		ui8_uartFlag = 1;
		HAL_UART_Receive_IT(&huart1, &ui8_rxData, 1);
	}
}
//---------------------------------------------------------------------------------

//-------------------- 2. UART Bluetooth Processing -------------------------------
void uart_handle(void)
{
	if (ui8_uartFlag && (signal_state == BLUETOOTH))
	{
		switch (ui8_rxData)
		{
			case 'S':
			{
				car_control(CAR_STOP_STATE, 0);
				break;
			}
			case 'F':
			{
				car_control(CAR_FORWARD_STATE, ui8_carSpeed);
				break;
			}
			case 'B':
			{
				car_control(CAR_BACKWARD_STATE, ui8_carSpeed);
				break;
			}
			case 'L':
			{
				car_control(CAR_LEFT_STATE, ui8_carSpeed);
				break;
			}
			case 'R':
			{
				car_control(CAR_RIGHT_STATE, ui8_carSpeed);
				break;
			}
			default:
			{
				if ('0' <= ui8_rxData && ui8_rxData <= '9')
				{
					ui8_carSpeed = (ui8_rxData - '0')*10;
				}
				break;
			}
		}
		ui8_uartFlag = 0;
	}
}
//----------------------------------------------------------------------------------

//------------------------------ 3. NRF24 Processing -------------------------------
void NRF24_handle(void)
{
	if(NRF24_available())
	{
		NRF24_read(c_myRxData, 32);
	}
	switch (c_myRxData[0])
	{
		case 'O':
		{
			signal_state = BLUETOOTH;
			break;
		}
		case 'S':
		{
			car_control(CAR_STOP_STATE, 0);
			break;
		}
		case 'F':
		{
			car_control(CAR_FORWARD_STATE, 95);
			break;
		}
		case 'B':
		{
			car_control(CAR_BACKWARD_STATE, 95);
			break;
		}
		case 'R':
		{
			car_control(CAR_RIGHT_STATE, 50);
			break;
		}
		case 'L':
		{
			car_control(CAR_LEFT_STATE, 50);
			break;
		}
	}
}
//----------------------------------------------------------------------------------

//------------------------- 4. KEYPAD 4x4 Processing -------------------------------
void KEYPAD_Handle(uint8_t key)
{
	switch (sys_state)
	{
		case NORMAL_STATE:
		{
			// No task
			// Car is controlling	
			break;
		}
		case LOCK_STATE:
		{
			if (key == 'D')
			{
				// Push D key to fill password
				sys_state = ENTER_LOCK_STATE;
				HAL_GPIO_TogglePin(GPIOC, GPIO_PIN_14);
			}
			break;
		}
		case ENTER_LOCK_STATE:
		{
			if ((key >= '0') && (key <= '9'))
			{
				if (key != ui8_keyLast)
				{
					if (ui8_index < 8)
					{
						arrui8_passBuff[ui8_index++] = key;
						HAL_GPIO_TogglePin(GPIOC, GPIO_PIN_14);
						ui8_keyLast = key;
						if (ui8_index == 8)
						{
							arrui8_passBuff[ui8_index] = '\0';
						}
					}
				}
			}
			else if (key == 'A')
			{
				// Push A key to check password
				if (strcmp((char *)arrui8_passBuff, (char *)arrui8_pass) == 0)
				{
					// Password correct
					sys_state = NORMAL_STATE;
					HAL_GPIO_WritePin(GPIOC, GPIO_PIN_13,GPIO_PIN_RESET);
				}
				else
				{
					sys_state = LOCK_30S_STATE;
					ui8_index = 0;
				}
				HAL_GPIO_TogglePin(GPIOC, GPIO_PIN_14);
			}
			break;
		}
		case LOCK_30S_STATE:
		{
			if (++ui32_timeLedErr >=20)
			{
				HAL_GPIO_TogglePin(GPIOC,GPIO_PIN_13);
				ui32_timeLedErr = 0;
			}
			// waiting 30 second
			if (++ui32_timeLock30s >= 1000)
			{
				memset(arrui8_passBuff, 0, PASS_LEN);
				sys_state = LOCK_STATE;
				HAL_GPIO_WritePin(GPIOC, GPIO_PIN_13, GPIO_PIN_SET);
				HAL_GPIO_WritePin(GPIOC, GPIO_PIN_14, GPIO_PIN_SET);
				ui32_timeLock30s = 0;
			}
			break;
		}
		default:
			
			break;
	}
}
//----------------------------------------------------------------------------------

//------------------------- 5. SysTick Interrupt -----------------------------------
void SysTick_Handler(void)
{
	HAL_IncTick();
	ui8_key = KEYPAD_GetKey();
	KEYPAD_Handle(ui8_key);
}
//----------------------------------------------------------------------------------

/* USER CODE END 0 */

/**
  * @brief  The application entry point.
  * @retval int
  */
int main(void)
{
  /* MCU Configuration--------------------------------------------------------*/

  /* Reset of all peripherals, Initializes the Flash interface and the Systick. */
  HAL_Init();

  /* Configure the system clock */
  SystemClock_Config();

  /* Initialize all configured peripherals */
  MX_GPIO_Init();
  MX_TIM1_Init();
  MX_USART1_UART_Init();
  MX_SPI2_Init();
  MX_TIM3_Init();
  /* USER CODE BEGIN 2 */

	// Initialize NRF24
	NRF24_begin(CEpin_GPIO_Port, CSNpin_Pin, CEpin_Pin, hspi2);
	
	NRF24_setAutoAck(false);
	NRF24_setChannel(52);
	NRF24_setPayloadSize(32);
	NRF24_openReadingPipe(1, ui64_rxPipeAddrs);
	NRF24_enableDynamicPayloads();
	NRF24_enableAckPayload();
	HAL_Delay(200);
	NRF24_startListening();
	
	// UART Recieve Interrupt 
	HAL_UART_Receive_IT(&huart1, &ui8_rxData, 1);
	
	// EOS Init with 5ms cycles interrupt
	EOS_Init(5);
	
	// Inittialize System state
	sys_state = LOCK_STATE;
	
	// Initialize Signal state
	signal_state = BLUETOOTH;
	
	// Initialize CAR Robot
	car_init(&htim1);
	HAL_GPIO_WritePin(GPIOC, GPIO_PIN_13, GPIO_PIN_SET);
	HAL_GPIO_WritePin(GPIOC, GPIO_PIN_15, GPIO_PIN_SET);
	HAL_GPIO_WritePin(GPIOC, GPIO_PIN_14, GPIO_PIN_SET);
	
  /* USER CODE END 2 */

  /* Infinite loop */
  /* USER CODE BEGIN WHILE */
  while (1)
  {
    /* USER CODE END WHILE */

    /* USER CODE BEGIN 3 */
		
		// Unclocking CAR
		if (sys_state == NORMAL_STATE)
		{
			// UART Bluetooth controlling car
			if (signal_state == BLUETOOTH)
			{
				uart_handle();
			}
			
			// NRF24 controlling car
			NRF24_handle();
		}
		
  }
  /* USER CODE END 3 */
}

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


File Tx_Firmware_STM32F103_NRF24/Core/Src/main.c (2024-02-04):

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
/* Includes ------------------------------------------------------------------*/
#include "main.h"

/* USER CODE BEGIN Includes */
#include "MY_NRF24.h"
#include "Button.h"
/* USER CODE END Includes */

/* USER CODE BEGIN PTD */
typedef enum
{
	OTHER,
	JOYSTICK_STA,
} JOYSTICK_state;
/* USER CODE END PTD */

ADC_HandleTypeDef hadc1;
DMA_HandleTypeDef hdma_adc1;

SPI_HandleTypeDef hspi1;

UART_HandleTypeDef huart1;

/* USER CODE BEGIN PV */
static Button_Typdef button_btn_1;
static JOYSTICK_state joy_state = OTHER;
static uint32_t JOYSTICK[2];

static uint64_t TxpipeAddrs = 0x11223344AA;
static char myTxData[32];

/* USER CODE END PV */

void SystemClock_Config(void);
static void MX_GPIO_Init(void);
static void MX_DMA_Init(void);
static void MX_SPI1_Init(void);
static void MX_USART1_UART_Init(void);
static void MX_ADC1_Init(void);
/* USER CODE BEGIN 0 */

// ---------------------------- 1. ADC Processing and Return control characters --------------------------
uint8_t JOYSTICK_handle(void)
{
	if ((JOYSTICK[0] >= 2000 && JOYSTICK[0] <= 3000) && (JOYSTICK[1] >= 2000 && JOYSTICK[1] <= 3000))
	{
		HAL_GPIO_WritePin(xmin_GPIO_Port, xmin_Pin, GPIO_PIN_SET);
		HAL_GPIO_WritePin(xplus_GPIO_Port, xplus_Pin, GPIO_PIN_SET);
		HAL_GPIO_WritePin(ymin_GPIO_Port, ymin_Pin, GPIO_PIN_SET);
		HAL_GPIO_WritePin(yplus_GPIO_Port, yplus_Pin, GPIO_PIN_SET);
		return 'S';	// STOP sigal from Tx device
	}
	
	if (JOYSTICK[0] < 2000 && JOYSTICK[1] >= 2000 && JOYSTICK[1] <= 3000)
	{
		HAL_GPIO_WritePin(xmin_GPIO_Port, xmin_Pin, GPIO_PIN_RESET);
		HAL_GPIO_WritePin(xplus_GPIO_Port, xplus_Pin, GPIO_PIN_SET);
		return 'R';	// RIGHT sigal from Tx device
	}
	
	if (JOYSTICK[0] > 3000 && JOYSTICK[1] >= 2000 && JOYSTICK[1] <= 3000)
	{
		HAL_GPIO_WritePin(xmin_GPIO_Port, xmin_Pin, GPIO_PIN_SET);
		HAL_GPIO_WritePin(xplus_GPIO_Port, xplus_Pin, GPIO_PIN_RESET);
		return 'L';	// LEFT sigal from Tx device
	}
	
	if (JOYSTICK[1] < 2000 && JOYSTICK[0] >= 2000 && JOYSTICK[0] <= 3000)
	{
		HAL_GPIO_WritePin(ymin_GPIO_Port, ymin_Pin, GPIO_PIN_RESET);
		HAL_GPIO_WritePin(yplus_GPIO_Port, yplus_Pin, GPIO_PIN_SET);
		return 'B';	// BACKWARD sigal from Tx device
	}
	
	if (JOYSTICK[1] > 3000 && JOYSTICK[0] >= 2000 && JOYSTICK[0] <= 3000)
	{
		HAL_GPIO_WritePin(ymin_GPIO_Port, ymin_Pin, GPIO_PIN_SET);
		HAL_GPIO_WritePin(yplus_GPIO_Port, yplus_Pin, GPIO_PIN_RESET);
		return 'F';	// FORWARD sigal from Tx device
	}
	return 0;
}
// -----------------------------------------------------------------------------------------------

// -------------- 2. Converting Button function bewteen Bluetooth and NRF24L01 --------------------
void	btn_pressing_callback(Button_Typdef *ButtonX)
{
	static uint8_t count_key = 0;
	switch (joy_state)
	{
		// Controll car by Bluetooth HC05
		case OTHER:
		{
			if (count_key == 0)
			{
				joy_state = JOYSTICK_STA;
				count_key = 1;
			}
			break;
		}
		// Controll car by NRF24L01
		case JOYSTICK_STA:
		{
			if (count_key == 1)
			{
				joy_state = OTHER;
				count_key = 0;
				// Initialize all LED used to indicate the direction for the user at default state
				HAL_GPIO_WritePin(xmin_GPIO_Port, xmin_Pin, GPIO_PIN_RESET);
				HAL_GPIO_WritePin(xplus_GPIO_Port, xplus_Pin, GPIO_PIN_RESET);
				HAL_GPIO_WritePin(ymin_GPIO_Port, ymin_Pin, GPIO_PIN_RESET);
				HAL_GPIO_WritePin(yplus_GPIO_Port, yplus_Pin, GPIO_PIN_RESET);
			}
			break;
		}
	}
	// Initialize a LED on car
	HAL_GPIO_TogglePin(GPIOB, GPIO_PIN_9);
}
// -----------------------------------------------------------------------------------------------


/* USER CODE END 0 */

/**
  * @brief  The application entry point.
  * @retval int
  */
int main(void)
{
  /* MCU Configuration--------------------------------------------------------*/

  /* Reset of all peripherals, Initializes the Flash interface and the Systick. */
  HAL_Init();

  /* Configure the system clock */
  SystemClock_Config();

  /* Initialize all configured peripherals */
  MX_GPIO_Init();
  MX_DMA_Init();
  MX_SPI1_Init();
  MX_USART1_UART_Init();
  MX_ADC1_Init();
  /* USER CODE BEGIN 2 */
	
	// Initialize a Button at PA2 to switch mode between Bluetoot HC05 and NRF24L01
	button_init(&button_btn_1, GPIOA, GPIO_PIN_2);
	
	// Initialize system state at Bluetooth HC05 mode
	joy_state = OTHER;
	
	// Initialize NRF24L01 in Transmit mode, noAck
	NRF24_begin(CEpin_GPIO_Port, CSNpin_Pin, CEpin_Pin, hspi1);

	
	NRF24_stopListening();
	NRF24_openWritingPipe(TxpipeAddrs);
	NRF24_setAutoAck(false);
	NRF24_setChannel(52);
	NRF24_setPayloadSize(32);
	
	NRF24_enableDynamicPayloads();
	NRF24_enableAckPayload();
	
	// Starting Calibration ADC
	HAL_ADCEx_Calibration_Start(&hadc1);
	
	// Starting DMA for ADC with 2 channel
	HAL_ADC_Start_DMA(&hadc1, JOYSTICK, 2); // Direct Memory Access
  /* USER CODE END 2 */

  /* Infinite loop */
  /* USER CODE BEGIN WHILE */
  while (1)
  {
    /* USER CODE END WHILE */

    /* USER CODE BEGIN 3 */
		
		// Polling 2 state
		switch (joy_state)
		{
			case OTHER:
			{
				// In Bluetooth mode
				NRF24_write("O", 32);
				HAL_Delay(50);
				break;
			}
			case JOYSTICK_STA:
			{
				// In NRF24L01 mode
				myTxData[0] = (char)JOYSTICK_handle();
				myTxData[1] = '\0';
				NRF24_write(myTxData, 32);
				HAL_Delay(50);
				break;
			}
		}
		// Polling button
		button_handle(&button_btn_1);
		
  }
  /* USER CODE END 3 */
}

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

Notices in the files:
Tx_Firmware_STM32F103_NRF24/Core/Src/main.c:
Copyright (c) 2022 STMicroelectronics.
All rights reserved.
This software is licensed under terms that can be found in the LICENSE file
